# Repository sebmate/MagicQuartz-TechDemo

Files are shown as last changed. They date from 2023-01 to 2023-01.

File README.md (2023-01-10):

# MagicQuartz Technology Demonstrator

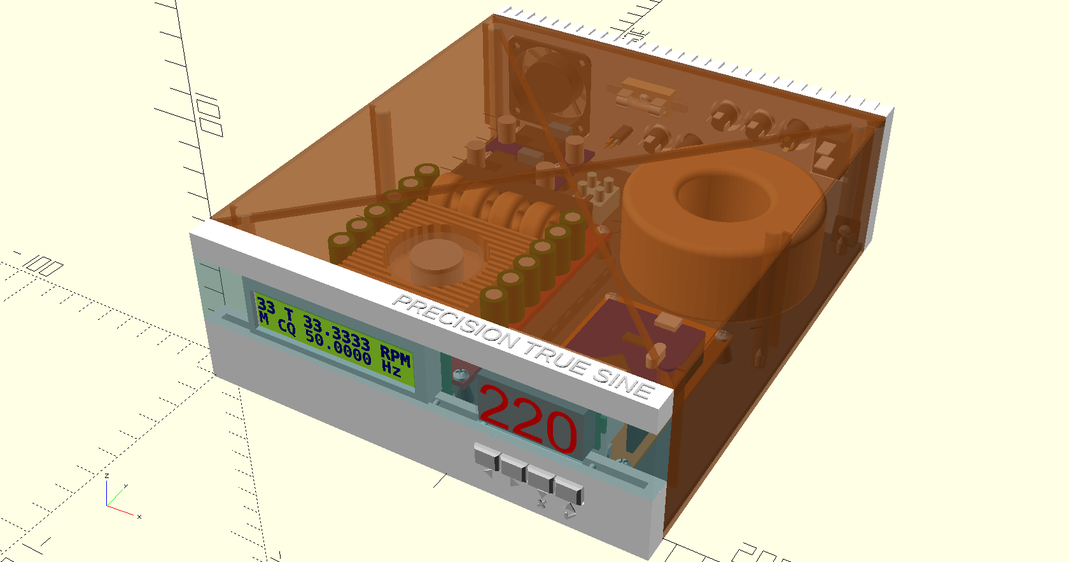
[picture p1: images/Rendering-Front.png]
MagicQuartz TechDemo Front Rendering


## Introduction

This repository contains an open source hardware design for a turntable speedbox that is capable of running the [MagicQuartz firmware](https://www.mate-labs.de). The speedbox, which is actually an ultra-precision true sine power inverter, actively regulates the AC frequency to control the turntable's speed. An optical sensor is used to measure the rotation speed of the turntable's platter.

The hardware design consits of two parts:

* An [OpenSCAD](https://openscad.org) model that can be used for generating 3D-printable parts and for making nice renderings of the device (as in the picture above). Note that the printing the enclosure is very time-consuming.
* A [KiCad](https://www.kicad.org) design for the mainboard (schematic and PCB). The PCB has been designed for rapid prototyping. While an optional second (top) copper layer may be used to improve shielding, the circuit can be fabricated single-sided using a small CNC or via etching. Of course, the board can also be fabricated by any PCB manufacturer.

Please note that the MagicQuartz firmware can also be run directly on standard Arduino hardware, such as an Arduino Mega 2560 Rev3 board and an LCD shield, or by using the Arduino's serial TTY. It is not necessary to build the device presented here to get started with the firmware. See [https://www.mate-labs.de](https://www.mate-labs.de) for details.

## Licensing

The information and files in this repository are provided under the CERN-OHL-S v2 open source license (please click [here](https://ohwr.org/project/cernohl/wikis/Documents/CERN-OHL-version-2) for details).

## Disclaimer

The purpose of this repository is to provide a technology demonstration that is near to a final product in terms of aesthetics, haptics, and functionality, but not necessarily in other terms, such as electrical safety, electromagnetic compliance (EMC), and others. No warranty of any sort can be given -- please review Section 6 of the [CERN-OHL-S v2](cern_ohl_s_v2.txt) license. Devices constructed on the basis of this design should never be considered fit for the end user.

If you build the device, you act on your own responsibility. Therefore, be sure to consider the following aspects: 

* Depending on the configuration (see below), the device may generate life-threatening, high voltages. Although great care was taken into account, its electrical safety has not been evaluated.
* The device may switch high currents using pulse width modulation (PWM), which may cause interference with other electronic devices and radio equipment. The electromagnetic compliance (EMC) has not been evaluated.
* The mechanical and thermal properties of the device, including fire safety, have not been evaluated. It should also be noted that the mechanical, electrical, and chemical properties of 3D-printed components may change and/or deteriorate over time.
* The technology demonstrator uses hardware components outside of their specifications and intended use. For example, an audio amplifier is used to step-up AC voltage via a transformer that is wired in reverse.
* Assembled devices based on the information presented here may only be used under supervision and under controlled conditions.

The information in this repository does not constitute assembly instructions. If you do not have sufficient knowledge (e.g. in electronics), do not attempt to build the device.

## Hardware Design

### Hardware Configurations

The design in this repository has been prepared to allow for the construction of various configurations. The table below contains a list of these.

| Type | Name | Description | Amplifier | Transformer | Power Supply | AC Voltmeter |
|---|---|---|---|---|---|---|
| 1 | Signal Generator Unit | Only generates a sine signal (one or two channels) that is routed to the "Signal Out" jack on the back panel. The amplifier and step-up stages may be part of another device. | No | No | 5V or direct USB | No |
| 2 | Single/Dual Phase Low Voltage Unit | As type 1, but with an additional power amplifier to drive a single or dual phase AC low voltage (e.g., 12V) turntable motor. The amplified signals are routed to the "Phase 1/2 Out" jacks. | Yes | No | Typ. 24-30V | Yes (low voltage)  |
| 3 | Single Phase High Voltage Unit | **Probably the most common variant**, for which this tech demo has been optimized. Generates a high voltage AC (110-220V) to drive a single phase turntable motor. The AC is routed to an external socket via the "AC Out 220V" (you may change this to 110V) cable on the back of the device. | Yes | Yes | Typ. 24-30V | Yes (high voltage) |
| 4 | Dual Phase High Voltage Unit | Because there isn't enough room in the design for a second transformer, the two transformers (one for each phase) should be placed in a second and third cabinet, into which the amplifier's high-power, low-voltage AC signals are routed. These "transformer-only" enclosures have yet to be designed, although a design based on the original one should be simple to create. | Yes | No | Typ. 24-30V | Yes |

### OpenSCAD 3D Model

The OpenSCAD file can be used to virtually explore the device and to create 3D printable parts.

Note: If the symbols on the front are not displayed correctly, the "Symbola" font has to be installed (Ubuntu package name: `fonts-symbola`).

#### Parts Overview and Printing Notes

The table below summarizes all 3D-printable parts of the 3D model along with some printing recommendations (these may be refined in the near future). The numbers are based on Cura 4.13.1 using an Ultimaker 2 (the old model, not the "Plus") and all recommendations below were based on the "Draft" profile.

While the STL files are available in the `release` folder for your convenience, they can be generated easily in OpenSCAD. Set the variable `render_components` to `false` and change the value of the variable `generate` to the respective part number. Then press F5 to preview the part, F6 to render the part, and F7 to export the STL file. The rendering may take a considerable amount of time. The generated objects are already properly oriented for printing.

In addition to the table below:

* Print all parts using "tree" support.
* Print all parts using "grid" infill pattern (except part 3, see notes).
* Print all parts with with 0.2 mm layer height (except part 8, see notes).
* Print all parts with with adhesion type "brim" (except part 8, see notes).

| Part Nr. | Name | Suggested Color | Notes / Exceptions | Printing Time | Total |
|---|---|---|---|---|---|
| 1 | Bottom Plate | Black | | 05:57 | 05:57 |
| 2 | Front Lower Part | White | | 02:40 | 02:40 |
| 3 | Front Center Part | Transparent | Use the "lightning" infill pattern to create a beautiful crystalline appearance. | 01:46 | 01:46 |
| 4 | Front Upper Part | White | | 01:08 | 01:08 |
| 5 | Cover | Brown | Decorative foil may not adhere properly to the edges, so I recommend the material saver variant. | 09:21 | |
| 5 | Cover (Material Saver) | Don’t Care | Cover the framework with thin cardboard (about as thick as a record sleeve) and then use decorative foil (e.g. wood grain). | 04:18 | 04:18 |
| 6 | Foot (Print 4x) | Silver | | 00:09 | 00:36 |
| 7 | Voltmeter Cover | Don’t Care | | 00:43 | 00:43 |
| 8 | Button Assembly | Silver | Print with 0.1 mm or less to improve strength, do not use adhesion support (brim). Enable ironing on top layer. | 00:39 | 00:39 |
| 9 | Back | White | | 04:03 | 04:03 |
| | | | | | 21:50 |

#### Assembly

All parts are held together with self-tapping screws type "DIN 7981 C H", 2.9x9.5 mm, except for the LCD and voltmeter cover, for which 2.2x9.5 mm are used. The DIN screws can of course also be replaced by similar compatible screws.

The three parts of the front panel (2-4) are held together via the LCD and the voltmeter cover.

The transformer and the internal fan (for amplifier type 2) are held down with cable ties. The bar in the middle of the housing can be used to attach cables with cable ties.

#### Components

The 3D model contains renderings of electrical or electronic components. These are visible if the `render_components` variable is set to `true`. Changing other variables, such as `amplifier_type`, may affect the appearance of some components ( such as the internal fan) in the rendering. Depending on the hardware configuration (see above) not all parts may be needed.

* **Mainboard**: The PCB for which the KiCad schematic and layout is available in this repository, see below.
* **Amplifier**: The design currently supports three amplifier types:
    * **TDA7498-based Amplifier (Type 1):** Nice design with fan, but quite expensive, requires higher DC voltage (29-30V), and dies regularly. There also seem to be cheaper copies, which are probably fakes. The good ones carry the brand name "SANWU".
    * **TPA3116D2-based Amplifier (Type 2):** Cheaply made, more noisy, and requires a better heat sink. But it works fine at 24V and seems to be more robust. Use an additional internal fan.
    * **Custom Amplifier (Type 3):** For future developments. Has the same size as the mainboard.
* **Transformer:** A toroidal transformer, e.g. 230V to 2x12V, 50VA. Must match the power configuration of the device. Used in reverse to step-up the voltage.
* **High Voltage Screw Terminal:** Connects the high voltage side of the transformer to the voltmeter and AC output cable on the back. The screw terminal can be glued to the bottom (pay attention to the electrical and hygroscopic properties of the glue) and additionally secured with cable ties after the cables are attached.
* **DC to DC Converters:** Serve to supply the mainboard (7V) and the fans. If the fans run well at 7V, you can connect the fans to the converter that supplies the mainboard; in this case, the second converter is not necessary.
* **Fans:** The fans should have a size of 40x40x10 mm. Using 12V fans makes sense, as they seem to run well with the mainboard's supply voltage (7V). The exhaust fan on the back has to be glued in so that the warm air is pulled out of the case. The internal fan (for amplifier type 2) is fixed with cable ties and blows onto the amplifier.
* **Fuse:** Used to protect the whole unit. Must match the power configuration of the device. When using a 50 VA transformer and a 24V/2A power supply, a 2A fuse (or a little less) should work. Please do the final math on your own.
* **LCD:** Standard 2x16 LCD.
* **Voltmeter:** A three-digit LED AC voltmeter, rated 60-300V, removed from its original housing. Type "YB27A". The voltmeter is live, thus there is a risk of electrical shock. When extending or replacing the wires, make sure that the new wires are qualified for the voltage rating and that everything is correctly isolated. 

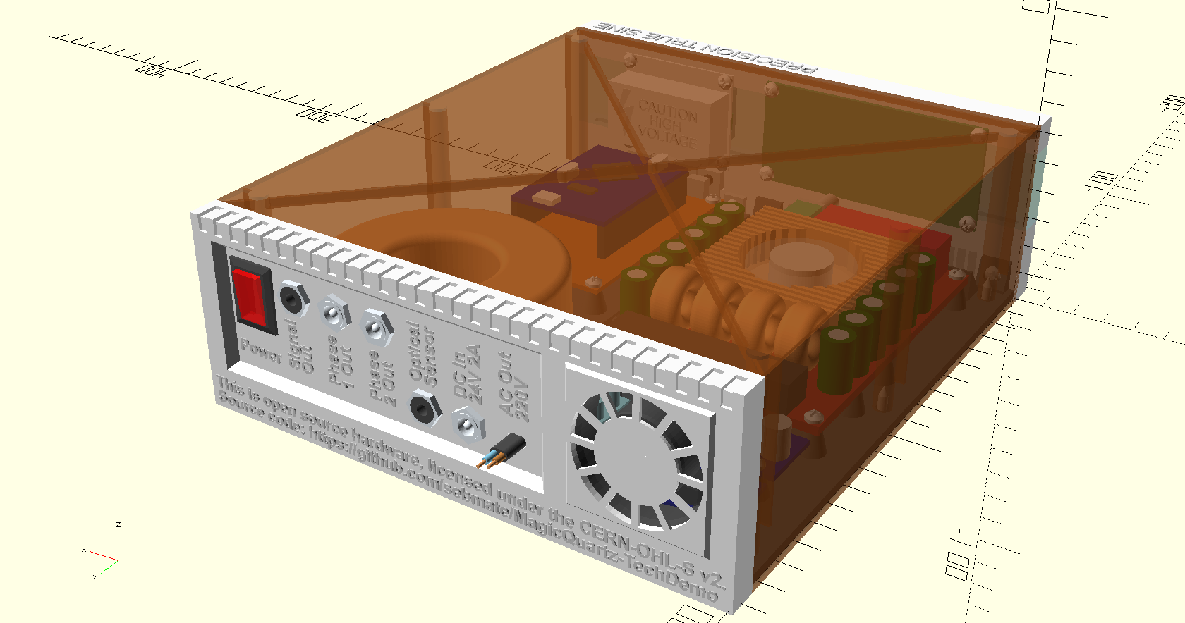
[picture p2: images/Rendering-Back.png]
MagicQuartz TechDemo Back Rendering


* **Back Panel:** The rear panel should be fully populated to block unwanted incoming airflow.
    * **Power Switch:** Used to turn the unit on and off. Type KCDI-101.
    * **Signal Out Jack:** 3.5 mm stereo socket that internally connects to the low-pass-filtered sine wave signal(s) that is/are generated by the mainboard.
    * **Phase 1 and 2 Out Jacks**: 5.5 / 2.5 mm DC power jacks that connect to the loudspeaker terminals of the amplifier.
    * **Optical Sensor Jack**: 3.5 mm stereo socket that provides the signal from the optical sensor to the mainboard.
    * **DC In Jack**: 5.5 / 2.5 mm DC power jack to which an external power plug (e.g. 220V AC to 24V DC) is connected.
    * **AC Out Cable Feedthrough**: Feedthrough for a cable connected to the high voltage screw terminal inside the device and providing a socket for the turntable at the other end.

### KiCad Schematic and PCB

In addition to the enclosure above, this repository also provides an electronic circuit, the "mainboard", which can run the MagicQuartz firmware and which can be built into the enclosure. The circuit implements a very simple digital to analog converter (DAC) based on an RC low-pass filter, which provides the sine signal to the digital amplifier. It also features an optional current sensing section, which allows the firmware to detect whether the turntable motor is currently powered or not ("Advanced Power Management", APM).

For the sake of simplicity, the design is build around the excellent "MEGA 2560 PRO" board (denoted U1 in the schematic). This board can be flashed with the MagicQuartz firmware easily via its USB interface and is plugged onto the mainboard, while making use of only the outer pins. Unlike other Arduino boards, this one has a real quartz oscillator, which ensures timing accuracy. 

To the best of my knowledge, this board was originally developed by a company called RobotDyn. Unfortunately, it seems to be no longer available, but re-makes by other companies are widely available. Click [here](https://web.archive.org/web/20211019002605/https://robotdyn.com/mega-2560-pro-embed-ch340g-atmega2560-16au.html) for an archived version of RobotDyn's webpage.

The PCB routing was done with the open source software FreeRouting (see [https://freerouting.org](https://freerouting.org)). 

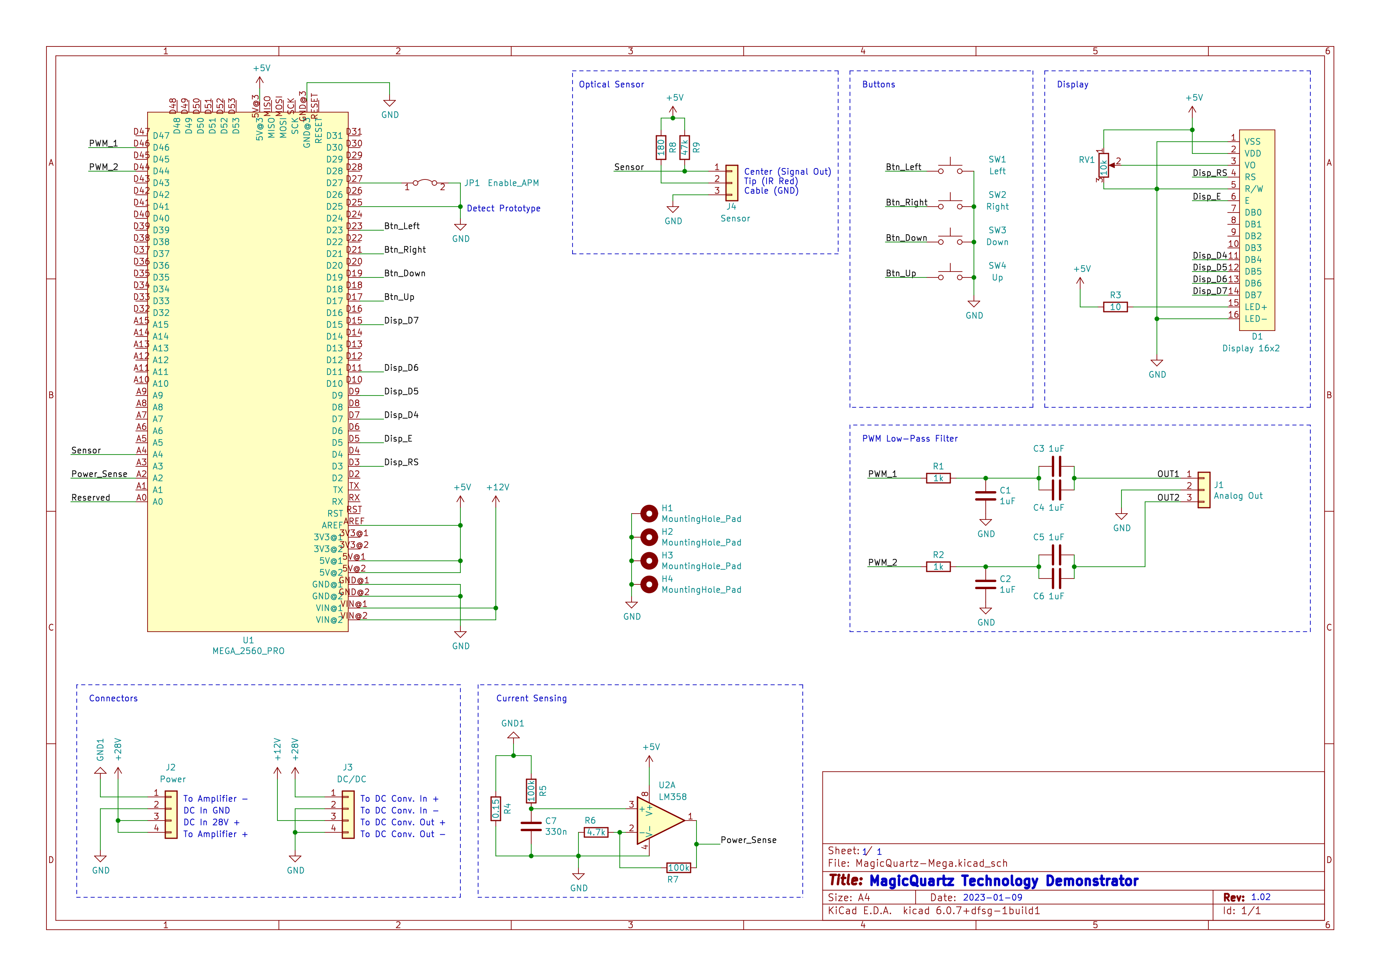
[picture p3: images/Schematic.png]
MagicQuartz TechDemo Schematic

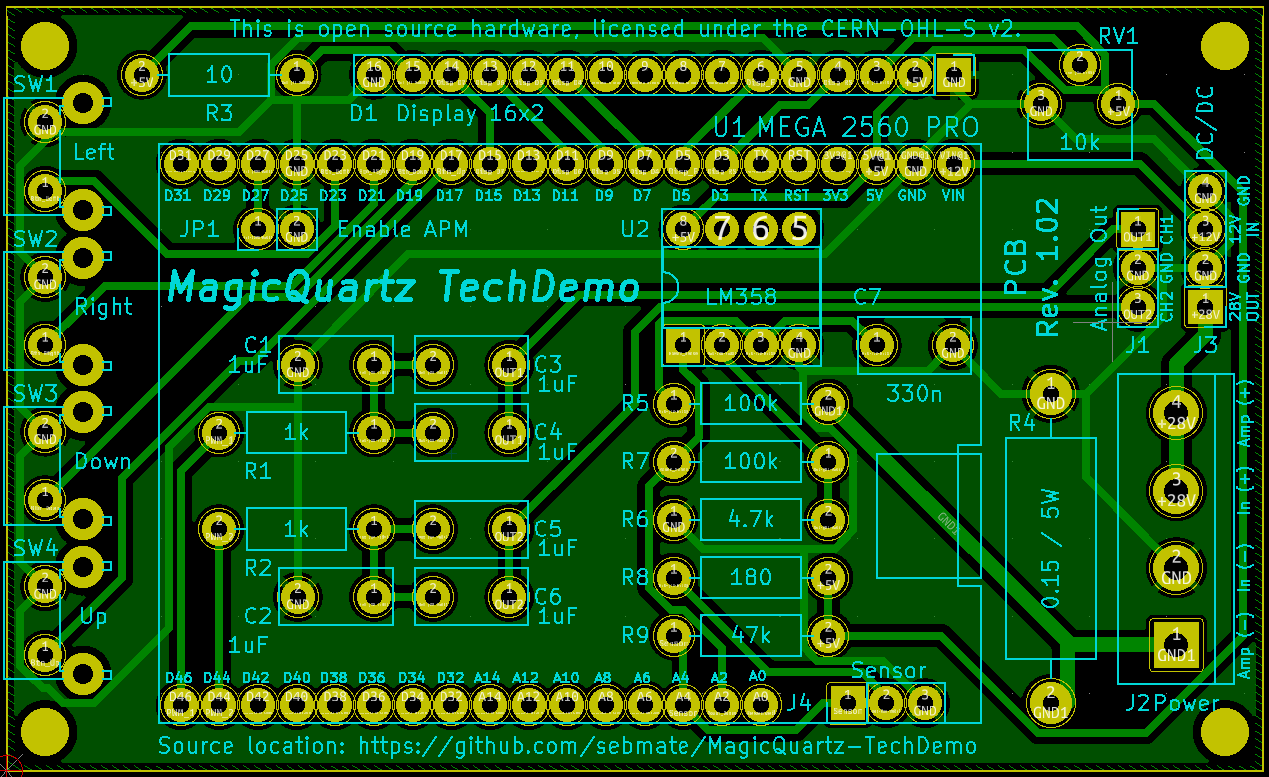
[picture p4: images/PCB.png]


#### Description of the circuit:

* The daughterboard U1, the "MEGA 2560 PRO" board, is powered via its internal voltage regulator from the nominal 12V rail, coming from one of the external DC-to-DC power converter boards via connector J3. As described above in section "Components", part "Fans", instead of using the nominal 12V, the voltage may be reduced to 7V, which allows one to also connect the fans to the same voltage regulator. The voltage should be at least 2V higher than the Arduino's 5V so that its voltage regulator works properly.
* The MagicQuartz firmware is / can be configured as follows:
    * Digital Pin D25 is pulled to GND to tell the firmware that it is not running on a standard Arduino board and using a display shield, but on the tech demo hardware instead. This reconfigures the firmware so that it can interface with the tech demo's display and buttons.
    * Digital Pin D27 is pulled to GND (jumper J1 "Enable APM" is closed), which tells the firmware that the current sensing circuit is available, which allows the firmware to detect whether the turntable motor is currently powered or not. The current measurement (see below) is optional.
* The current measurement works as follows: The current of the power section (the digital amplifier board) is measured via the voltage drop across resistor R4 (0.15 Ohm, 5 Watt). The measured voltage is low-pass filtered via C7 and R5 and brought via the operational amplifier U2A to a voltage range that can be measured by the microcontoller running the MagicQuartz firmware.
* The PWM low-pass filter section converts the PWM signals from the microcontroller into one or two analog sine waves using simple RC filters. The filters are designed to have a cutoff frequency of about 200 Hz, which is high enough to pass the generated AC frequency but block the PWM noise. The filter is implemented twice in case a two-phase inverter configuration is to be implemented (cf. "Type 4" in section "Hardware Configurations" above). In single-phase configurations, only one filter may be populated and the mono signal should be fed to both stereo channels of the digital amplifier.

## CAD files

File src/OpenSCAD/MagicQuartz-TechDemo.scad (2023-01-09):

//  ------------------------------------------------------------------------------
// | Copyright Sebastian Mate 2022.                                               |
// |                                                                              |
// | This source describes Open Hardware and is licensed under the CERN-OHL-S v2. |
// |                                                                              |
// | You may redistribute and modify this source and make products using it under |
// | the terms of the CERN-OHL-S v2 (https://ohwr.org/cern_ohl_s_v2.txt).         |
// |                                                                              |
// | This source is distributed WITHOUT ANY EXPRESS OR IMPLIED WARRANTY,          |
// | INCLUDING OF MERCHANTABILITY, SATISFACTORY QUALITY AND FITNESS FOR A         |
// | PARTICULAR PURPOSE. Please see the CERN-OHL-S v2 for applicable conditions.  |
// |                                                                              |
// | Source location: https://github.com/sebmate/MagicQuartz-TechDemo             |
// |                                                                              |
// | As per CERN-OHL-S v2 section 4, should You produce hardware based on this    |
// | source, You must where practicable maintain the Source Location visible      |
// | on the external case of the device or other products you make using this     |
// | source.                                                                      |
//  ------------------------------------------------------------------------------

$fn=64;

render_components = true; // Set this to false to generate the 3D-printable model, then press F6 to render and finally export the STL.

transparancy_cover = 0.5; // 0 = hidden, 0.5 = transparent, 1 = solid

amplifier_type = 1; // Which amplifier to render (1 or 2)

generate = 0; // Which part to render (0-9, see list below)

// 0 = Whole unit (for rendering only!)
// 1 = Bottom plate
// 2 = Front lower part
// 3 = Front center part (transparent)
// 4 = Front upper part
// 5 = Cover
// 6 = Foot (print 4 times)
// 7 = Voltmeter cover
// 8 = Button assembly
// 9 = Back

material_saver = true; // The effect is only visible when generating the distinct parts
material_saver_grid_bar_step = 15; // Must touch all elements
material_saver_grid_bar_width = 0.8;
material_saver_grid_bar_height = 1.5;
material_saver_bottom_height = 0.4; // Should be at least two layers

sacrificial_layer_height = -0.01;

// All screws are of type "DIN 7981 C H", 2.9x9.5, except for the LCD, which uses "2.2x9.5"
screw_shaft_diameter = 2.9;
screw_shaft_diameter_lcd = 2.2; // 2.2 for the display screws
screw_shaft_length = 9.5;
screw_head_diameter_min = 5.3;
screw_head_diameter_typ = 5.4;
screw_head_diameter_max = 5.6;
screw_head_hight_min = 1.95;
screw_head_hight_max = 2.20;

// Tuneable parameters:
screw_holder_hight = screw_shaft_length + 1;
case_bottom_height = 3;

// Colors:
color_transformer = "SandyBrown";
color_screw = "AliceBlue";
color_cover = "SaddleBrown";
color_buttons = "Silver";
color_bottom = [0.3, 0.3, 0.3];

// Default color scheme (transparent front center part):
color_case = "White";
color_front_center = "CadetBlue";
transparency_front_center = 0.6;
transparency_voltmeter_window_window = 0.1;

// Alternative color scheme (opaque front center part):
//color_case = "Silver";
//color_front_center = "White";
//transparency_front_center = 1;
//transparency_voltmeter_window_window = 1;

pcb_mainboard_pos_x = 106.5;  // Dermined by the visual tests (see below). Should align with voltmeter.
pcb_mainboard_pos_y = 8; // Buttons pretrude 6 mm + 2 mm for button assembly

high_voltage_screw_terminal_holder_pos_x = 69;
high_voltage_screw_terminal_holder_pos_y = 150;

// Transformer:
transformer_height = 34;
transformer_pos_x = 130;
transformer_pos_y = 140;
transformer_diameter_outer = 78;
transformer_diameter_inner = 35;
transformer_corner = 6;

// Display (DISPLAYTECH 162) (rotated!):
display_frame_size_x = 74; 
display_frame_size_y = 25;
display_frame_size_z = 8.5;

// Case outer dimensions:
case_size_width = transformer_pos_x + (transformer_diameter_outer / 2) + 5;
case_size_depth = transformer_pos_y + (transformer_diameter_outer / 2) + 5;   
front_depth = display_frame_size_z + 1.5;
front_lower_height = 25;
front_center_height = display_frame_size_y + 2;
front_upper_height = 10;
front_width = case_size_width;

front_height = front_lower_height + front_center_height + front_upper_height;

back_depth = 10;
back_height = front_height;
back_width = case_size_width;

cover_screw_distance = 6;

cable_tie_thickness = 1;
cable_tie_width = 5;

cover_top_height = 1;
cover_edges_size = 3;
cover_rigidity_grid_height = 6;

// Feet:
foot_size_x = 25;
foot_size_z = 5;
felt_glider_size_x = 20;
felt_glider_size_z = 3.5;
feet_front_distance_x = 30;
feet_front_distance_y = 30;
feet_back_distance_x = case_size_width - transformer_pos_x;
feet_back_distance_y = case_size_depth - transformer_pos_y;

// Front:
voltmeter_windowpane_thickness = 0.4;
buttons_bending_part_thickness = 0.4;

// Calculate positions of LCD and voltmeter on front:
two_line_display_visible_width = 64.5;
two_line_display_visible_shift_x = 8;
voltmeter_visible_width = 37.7;
voltmeter_visible_shift_x = 1.35;
space_between_parts = ((front_width + 2) - two_line_display_visible_width - voltmeter_visible_width) / 3;
two_line_display_pos_x = space_between_parts - two_line_display_visible_shift_x - 1;
voltmeter_pos_x = (space_between_parts * 2) + two_line_display_visible_width - voltmeter_visible_shift_x - 1;

// Simple visual test to check that the spacing is correct:

//translate([-1, -15, 15]) cube([space_between_parts, 10, 25]);
//translate([-1 + space_between_parts + two_line_display_visible_width, -15, 15]) cube([space_between_parts, 10, 25]);
//translate([-1 + space_between_parts + two_line_display_visible_width + space_between_parts + voltmeter_visible_width, -15, 15]) cube([space_between_parts, 10, 25]);

// ========================== COMPONENT RENDERINGS ==========================

module Fuse_Holder(mode) { // for 5x20 fuses

   translate([0, 0, 4]) Screw(mode, 3, screw_shaft_diameter);
   if (mode == 3 || mode == 4) {

        color("LightGray") difference() {
            translate([0, 0, 4]) {
                hull() {
                translate([-17, 0, 0]) cylinder(d=4, h=0.3, center = true);
                translate([17, 0, 0]) cylinder(d=4, h=0.3, center = true);
                }
            }
            translate([0, 0, 5.9 / 2]) Screw(2, 3, screw_shaft_diameter);
        }       
        color("Moccasin") difference() {
            translate([0, 0, 5.9 / 2]) cube([22, 10.3, 5.9], center = true);
            translate([0, 0, 5.9 / 2]) Screw(2, 3, screw_shaft_diameter);
        }

        translate([0, 0, 10]) rotate([-90, 0, 0]) rotate([0, 90, 0]) {
            color("AliceBlue") translate([0, 0, 7.501]) cylinder(d = 5, h = 5, center = true);
            color("AliceBlue") translate([0, 0, -7.501]) cylinder(d = 5, h = 5, center = true);
            color("White", 0.5) cylinder(d = 4.5, h = 20, center = true);
            color("LightGray") translate([-2.6, 3, 7.7]) cube([0.5, 10, 5], center = true);
            color("LightGray") translate([-2.6, 3, -7.7]) cube([0.5, 10, 5], center = true);
            color("LightGray") translate([2.6, 3, 7.7]) cube([0.5, 10, 5], center = true);
            color("LightGray") translate([2.6, 3, -7.7]) cube([0.5, 10, 5], center = true);
        }
    }
}

module Power_Cord(mode) {
    cable_length = 30;
    if (mode == 3 || mode == 4) {
        color([0.3, 0.3, 0.3]) hull() {
            translate([1.15, 0, 0]) cylinder(d = 3.3, h = cable_length * 0.85, center = true);
            translate([-1.15, 0, 0]) cylinder(d = 3.3, h = cable_length * 0.85, center = true);
        }
        color("Peru") translate([1.15, 0, -cable_length / 50]) cylinder(d = 2, h = cable_length * 1.1, center = true);
        color("SkyBlue") translate([-1.15, 0, cable_length / 50]) cylinder(d = 2, h = cable_length * 1.1, center = true);
        color("SandyBrown") translate([1.15, 0, -cable_length / 50]) cylinder(d = 1, h = cable_length * 1.3, center = true);
        color("SandyBrown") translate([-1.15, 0, cable_length / 50]) cylinder(d = 1, h = cable_length * 1.3, center = true);
    }
    if (mode == 2 || mode == 4) {
        color(color_case) hull() {
            translate([1.15, 0, 0]) cylinder(d = 3.3 + 0.6, h = cable_length * 0.85, center = true);
            translate([-1.15, 0, 0]) cylinder(d = 3.3 + 0.6, h = cable_length * 0.85, center = true);
        }
    }
}
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

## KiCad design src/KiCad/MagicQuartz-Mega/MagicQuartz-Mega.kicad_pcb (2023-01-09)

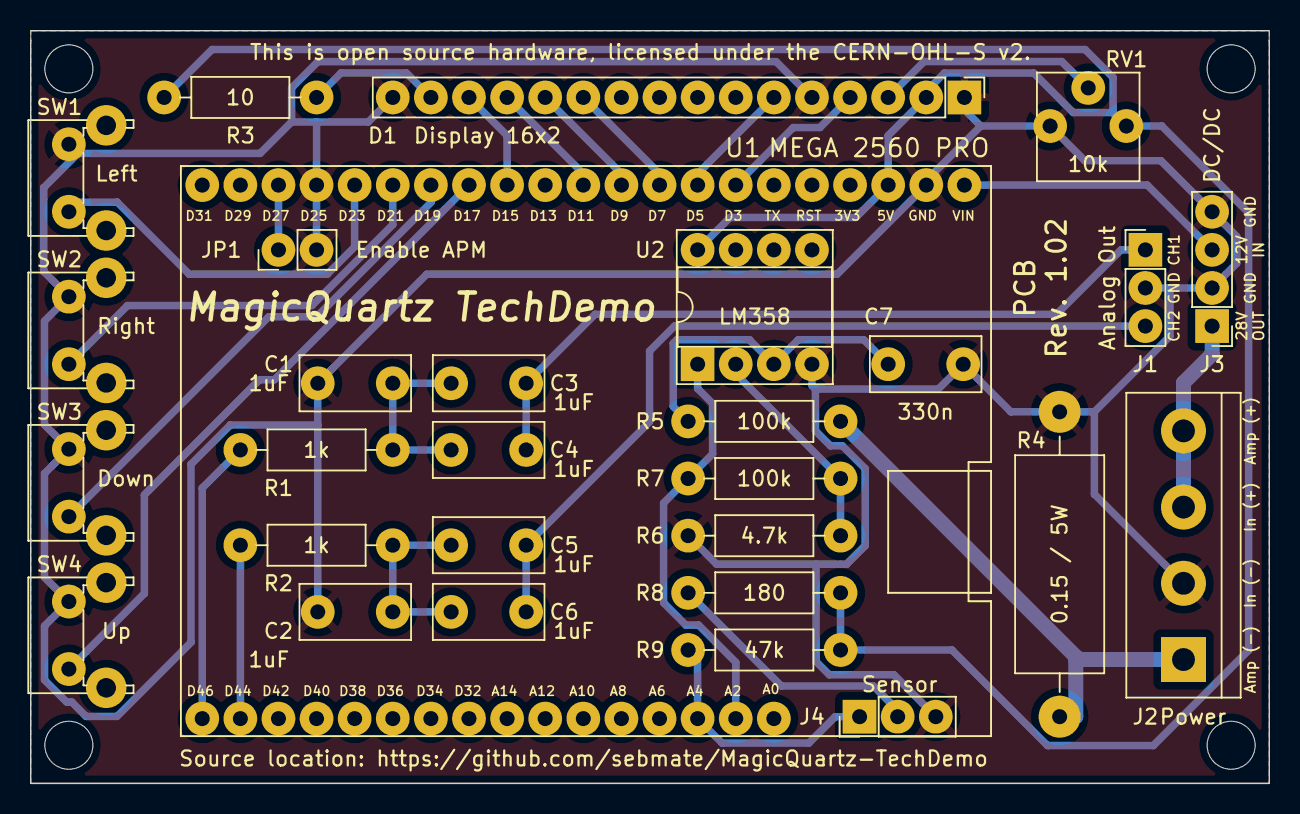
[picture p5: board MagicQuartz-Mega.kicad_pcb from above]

Board: 2 copper layers, 82.6 x 50.2 mm, 33 parts (0 on the bottom side), 29 nets.

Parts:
C1, C2, C3, C4, C5, C6: 1uF; C_Rect_L7.2mm_W3.5mm_P5.00mm_FKS2_FKP2_MKS2_MKP2
C7: 330n; C_Rect_L7.2mm_W3.5mm_P5.00mm_FKS2_FKP2_MKS2_MKP2
D1: Display 16x2; PinHeader_1x16_P2.54mm_Vertical
H1, H2, H3, H4: MountingHole_Pad; MountingHole_3.2mm_M3
J1: Analog Out; PinHeader_1x03_P2.54mm_Vertical
J2: Power; TerminalBlock_bornier-4_P5.08mm
J3: DC/DC; PinHeader_1x04_P2.54mm_Vertical
J4: Sensor; PinHeader_1x03_P2.54mm_Vertical
JP1: Enable APM; PinHeader_1x02_P2.54mm_Vertical
R1, R2: 1k; R_Axial_DIN0207_L6.3mm_D2.5mm_P10.16mm_Horizontal
R3: 10; R_Axial_DIN0207_L6.3mm_D2.5mm_P10.16mm_Horizontal
R4: 0.15 / 5W; R_Axial_DIN0614_L14.3mm_D5.7mm_P20.32mm_Horizontal
R5, R7: 100k; R_Axial_DIN0207_L6.3mm_D2.5mm_P10.16mm_Horizontal
R6: 4.7k; R_Axial_DIN0207_L6.3mm_D2.5mm_P10.16mm_Horizontal
R8: 180; R_Axial_DIN0207_L6.3mm_D2.5mm_P10.16mm_Horizontal
R9: 47k; R_Axial_DIN0207_L6.3mm_D2.5mm_P10.16mm_Horizontal
RV1: 10k; Potentiometer_Vishay_T73YP_Vertical
SW1: Left; SW_Tactile_SPST_Angled_PTS645Vx83-2LFS
SW2: Right; SW_Tactile_SPST_Angled_PTS645Vx83-2LFS
SW3: Down; SW_Tactile_SPST_Angled_PTS645Vx83-2LFS
SW4: Up; SW_Tactile_SPST_Angled_PTS645Vx83-2LFS
U1: MEGA 2560 PRO; MEGA2560PRO-Reduced
U2: LM358; DIP-8_W7.62mm_Socket

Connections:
+5V: D1.2 (VDD), R3.2, R8.2, R9.2, RV1.1, U1.5V@1, U2.8 (V+)
+12V: J3.3, U1.VIN@1
+28V: J2.3, J2.4, J3.1
/Btn_Down: SW3.1, U1.D19
/Btn_Left: SW1.1, U1.D23
/Btn_Right: SW2.1, U1.D21
/Btn_Up: SW4.1, U1.D17
/Disp_D4: D1.11 (DB4), U1.D7
/Disp_D5: D1.12 (DB5), U1.D9
/Disp_D6: D1.13 (DB6), U1.D11
/Disp_D7: D1.14 (DB7), U1.D15
/Disp_E: D1.6 (E), U1.D5
/Disp_RS: D1.4 (RS), U1.D3
/OUT1: C3.1, C4.1, J1.1
/OUT2: C5.1, C6.1, J1.3
/PWM_1: R1.2, U1.D46
/PWM_2: R2.2, U1.D44
/Power_Sense: R7.2, U1.A2, U2.1
/Sensor: J4.1, R9.1, U1.A4
GND: C1.2, C2.2, C7.2, D1.1 (VSS), D1.5 (R/W), D1.16 (LED-), J1.2, J2.2, J3.2, J3.4, J4.3, JP1.2 (B), R4.1, R6.1, RV1.3, SW1.2, SW2.2, SW3.2, SW4.2, U1.D25, U1.GND@1, U2.4 (V-)
GND1: J2.1, R4.2, R5.2
unnamed: C1.1, C3.2, C4.2, R1.1
unnamed: C2.1, C5.2, C6.2, R2.1
unnamed: C7.1, R5.1, U2.3 (+)
unnamed: D1.3 (VO), RV1.2
unnamed: D1.15 (LED+), R3.1
unnamed: J4.2, R8.1
unnamed: JP1.1 (A), U1.D27
unnamed: R6.2, R7.1, U2.2 (-)

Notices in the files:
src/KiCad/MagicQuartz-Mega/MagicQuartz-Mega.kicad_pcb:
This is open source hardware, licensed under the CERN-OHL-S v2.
